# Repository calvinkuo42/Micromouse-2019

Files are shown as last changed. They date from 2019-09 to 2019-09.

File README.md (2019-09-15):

# Micromouse-2019

IEEE Micromouse project I did with Philip Kwan and Sean Chen at UCLA over the 2018-19 school year. We began with a STM32 Nucleo Development board and assembled a demo from a previously designed kit. We then programmed the hardware using C on mbed. A similar code was used to control the "mouse" we later designed ourselves (schematic and board).

Micromouse: https://en.wikipedia.org/wiki/Micromouse

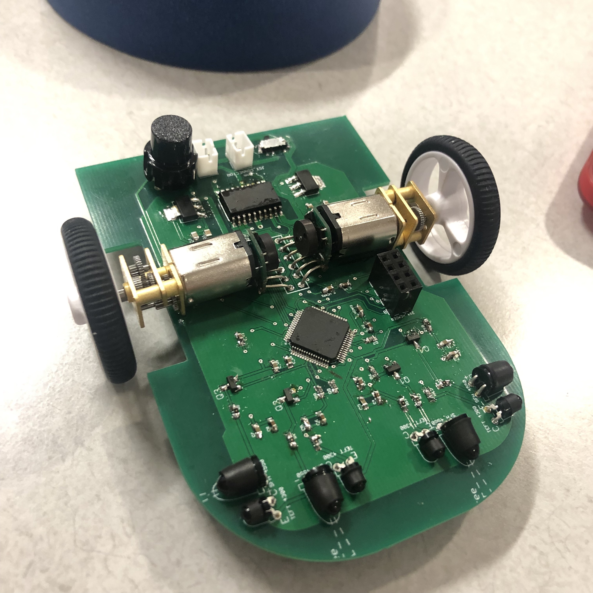
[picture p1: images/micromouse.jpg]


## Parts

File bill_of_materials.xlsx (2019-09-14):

Category | Part No. (Manufacturer) | Package | Vendor | Vendor No. | Description | Qty. | Unit Price | Total Price | Vendor Link
Transistor | SFH 309 | 5mm | Mouser | 720-SFH309 | ir_receiver | 8 | $0.39 | $3.12 | https://www.mouser.com/ProductDetail/OSRAM-Opto-Semiconductors/SFH-309
LED | SFH 4550 | 5mm | Mouser | 720-SFH4550 | ir_emitter | 10 | $0.80 | $8.00 | https://www.mouser.com/ProductDetail/OSRAM-Opto-Semiconductors/SFH-4550
H-Bridge | L293DD | so20 | Mouser | 511-L293DD | motor_driver | 2 | $3.83 | $7.66 | https://www.mouser.com/ProductDetail/STMicroelectronics/L293DD
Other IC | AZ1117EH-3.3TRG1 | so223 | Digi-Key | AZ1117EH-3.3TRG1DICT-ND | voltage_regulator | 4 | $0.43 | $1.72 | https://www.digikey.com/product-detail/en/diodes-incorporated/AZ1117EH-3.3TRG1/AZ1117EH-3.3TRG1DICT-ND/5001336
Other IC | AZ1117EH-5.0TRG1 | so223 | Digi-Key | AZ1117EH-5.0TRG1DICT-ND | voltage_regulator | 4 | $0.43 | $1.72 | https://www.digikey.com/product-detail/en/diodes-incorporated/AZ1117EH-5.0TRG1/AZ1117EH-5.0TRG1DICT-ND/5001335
Other | none | none | Pololu | 3081 | encoder | 2 | $8.95 | $17.90 | https://www.pololu.com/product/3081
MCU | STM32F405RGT6 | lqfp64 | Digi-Key | 497-11767-ND | microcontroller | 1 | $10.58 | $10.58 | https://www.digikey.com/product-detail/en/STM32F405RGT6/497-11767-ND/2754208?WT.z_slp_buy=stm_stm32f4
Other | none | none | Pololu | 2378 | motor | 2 | $16.95 | $33.90 | https://www.pololu.com/product/2378
Other | none | none | Pololu | 989 | motor_bracket | 1 | $4.99 | $4.99 | https://www.pololu.com/product/989
Transistor | CMPDM7002AHC TR | SOT-23 | Digi-Key | CMPDM7002AHCCT-ND | mosfet | 5 | $0.70 | $3.50 | https://www.digikey.com/product-detail/en/central-semiconductor-corp/CMPDM7002AHC-TR/CMPDM7002AHCCT-ND/5324492
Capacitor | C0805T105K4RACTU | 805 | Mouser | 80-C0805T105K4RACTU | capacitor | 8 | $2.06 | $16.48 | https://www.mouser.com/ProductDetail/KEMET/C0805T105K4RACTU
Capacitor | 06035J0R1PBSTR | 603 | Mouser | 581-06035J0R1PBSTR | capacitor | 8 | $1.94 | $15.52 | https://www.mouser.com/ProductDetail/AVX/06035J0R1PBSTR
Capacitor | 06035J0R1PBSTR | 603 | Mouser | 81-ZRB18AR6YA475KE5L | capacitor | 8 | $0.37 | $2.96 | https://www.mouser.com/ProductDetail/AVX/06035J0R1PBSTR
Capacitor | GRM188R6YA225KA12D | 603 | Mouser | 81-GRM188R6YA225KA2D | capacitor | 4 | $0.21 | $0.84 | https://www.mouser.com/ProductDetail/Murata-Electronics/GRM188R6YA225KA12D
Resistor | RK73H1ERTTP3301D | 402 | Mouser | 660-RK73H1ERTTP3301D | resistor | 3 | $0.41 | $1.23 | https://www.mouser.com/ProductDetail/KOA-Speer/RK73H1ERTTP3301D
Resistor | RC0201JR-071KL | 603 | Mouser | 603-RC0201JR-071KL | resistor | 12 | $1.05 | $12.60 | https://www.mouser.com/ProductDetail/Yageo/RC0201JR-071KL
Resistor | RC0201FR-0751RL | 603 | Mouser | 603-RC0201FR-0751RL | resistor | 8 | $0.10 | $0.80 | https://www.mouser.com/ProductDetail/Yageo/RC0201FR-0751RL?qs=sGAEpiMZZMvdGkrng054t219Tlw6YGVDLY9pioqn68o%3d
Resistor | RC0201JR-0747KL | 603 | Mouser | 603-RC0201JR-0747KL | resistor | 8 | $0.10 | $0.80 | https://www.mouser.com/ProductDetail/Yageo/RC0201JR-0747KL
Switch/Button | SSSS811101 | spdt | Mouser | 688-SSSS811101 | switch | 1 | $0.97 | $0.97 | https://www.mouser.com/ProductDetail/ALPS/SSSS811101
Switch/Button | SKPMANE010 | none | Mouser | 688-SKPMAN | button | 1 | $0.57 | $0.57 | https://www.mouser.com/ProductDetail/ALPS/SKPMANE010/
Headers/Connectors | S2B-PH-K-S(LF)(SN) | none | Digi-Key | 455-1719-ND | jst | 2 | $0.17 | $0.34 | https://www.digikey.com/product-detail/en/jst-sales-america-inc/S2B-PH-K-S(LF)(SN)/455-1719-ND/926626&
Headers/Connectors | none | none | Pololu | 1024 | 2x4 header | 1 | $0.59 | $0.59 | https://www.pololu.com/product/1024
 |  |  |  |  |  |  |  | $0.00
 |  |  |  |  |  |  |  | $0.00
 |  |  |  |  |  |  |  | $0.00
 |  |  |  |  |  |  |  | $0.00
 |  |  |  |  |  |  |  | $0.00
 |  |  |  |  |  |  |  | $0.00
 |  |  |  |  |  |  |  | $0.00
 |  |  |  |  |  |  |  | $0.00
 |  |  |  |  |  |  |  | $0.00
 |  |  |  |  |  |  |  | $0.00
 |  |  |  |  |  |  |  | $0.00
 |  |  |  |  |  |  |  | $0.00
 |  |  |  |  |  |  |  | $0.00
 |  |  |  |  |  |  |  | $0.00
 |  |  |  |  |  |  |  | $0.00
 |  |  |  |  |  |  |  | $0.00
 |  |  |  |  |  |  |  | $0.00
 |  |  |  |  |  |  |  | $0.00
 |  |  |  |  |  |  |  | $0.00
 |  |  |  |  |  |  |  | $0.00
 |  |  |  |  |  |  |  | $0.00
 |  |  |  |  |  |  |  | $0.00
 |  |  |  |  |  |  |  | $0.00
 |  |  |  |  |  | ADAFRUIT: | $0.0000
 |  |  |  |  |  | AMAZON: | $0.0000
 |  |  |  |  |  | DIGIKEY: | $0.0000
 |  |  |  |  |  | MOUSER: | $71.5500
 |  |  |  |  |  | POLOLU: | $57.3800
 |  |  |  |  |  | SPARKFUN: | $0.0000
 |  |  |  |  |  | TOTAL: | $128.9300

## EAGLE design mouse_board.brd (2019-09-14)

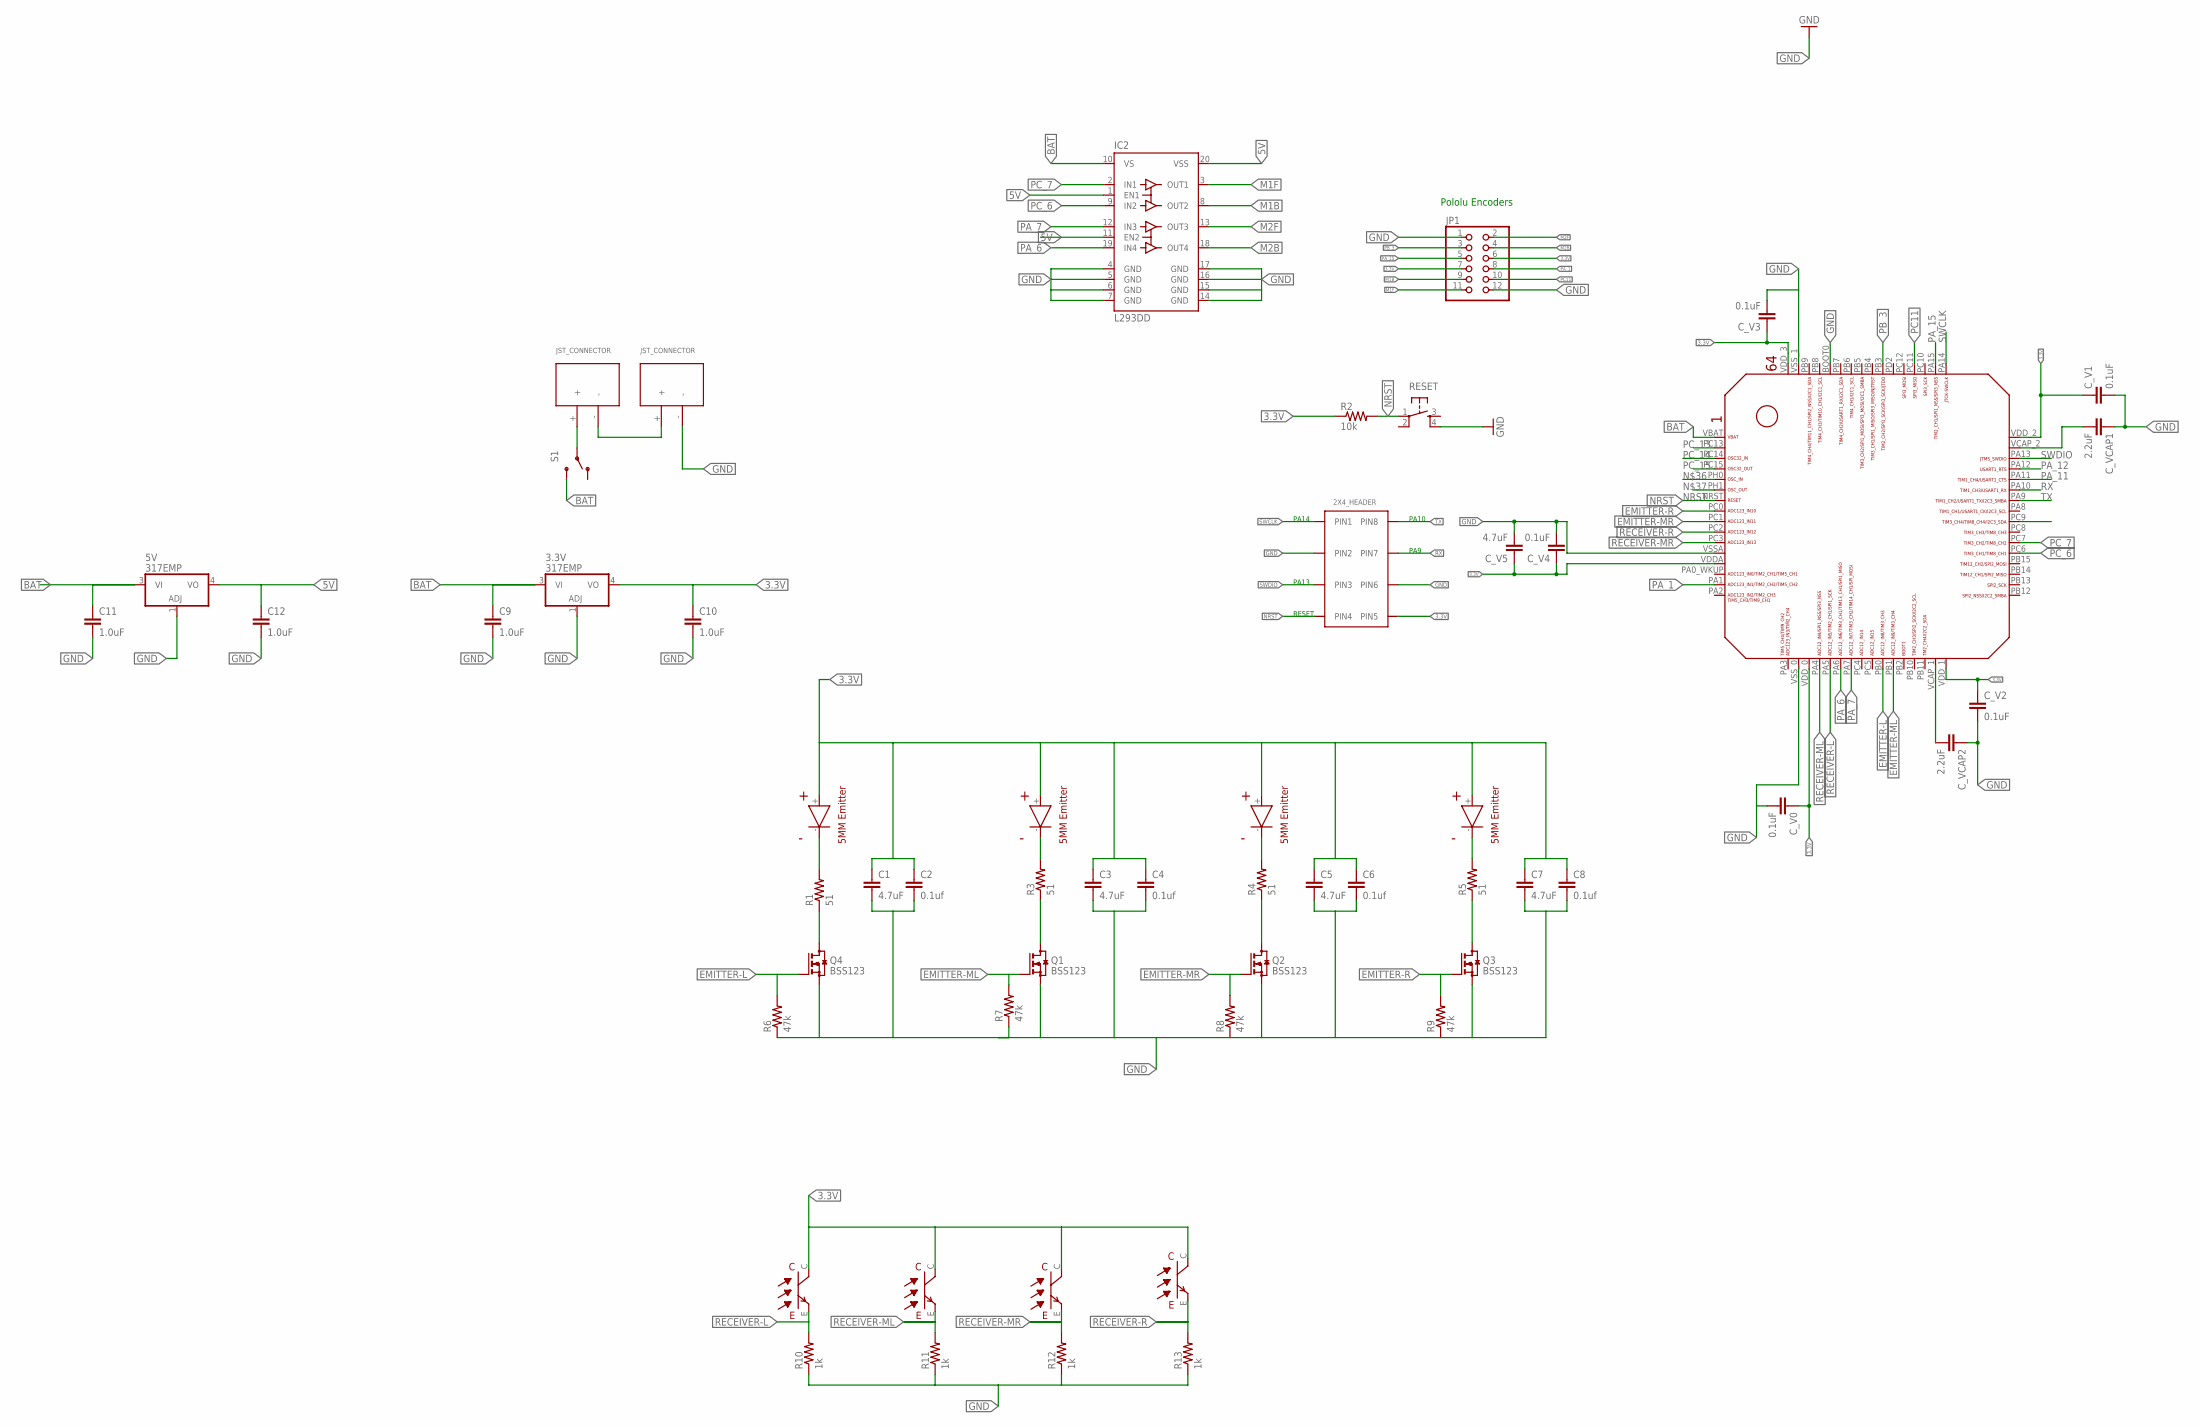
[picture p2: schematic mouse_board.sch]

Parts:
3.3V, 5V: 317EMP; SOT223
BATTERY1, BATTERY2: JST_CONNECTOR_FEMALE
C1, C3, C5, C7: 4.7uF; 0603-CAP
C2, C4, C6, C8: 0.1uf; 0603-CAP
C9, C10, C11, C12: 1.0uF; 0603-CAP
C_V0, C_V1, C_V2, C_V3, C_V4: 0.1uF; 0603-CAP
C_V5: 4.7uF; 0603-CAP
C_VCAP1, C_VCAP2: 2.2uF; 0603-CAP
IC2: L293DD; SO20
JP1: PINHD-2X6; 2X06
MCU/BLU: 2X3_HEADER
Q1, Q2, Q3, Q4: BSS123; SOT23
R1, R3, R4, R5: 51; 0603-RES
R2: 10k; 0603-RES
R6, R7, R8, R9: 47k; 0603-RES
R10, R11, R12, R13: 1k; 0603-RES
RESET: TAC_SWITCHPTH; TACTILE-PTH
S1: SWITCH-SPST-SMD-A
U$1: STM32F405/415_LQFP64
U$2, U$3, U$4, U$5: EMITTER
U$6, U$7, U$8, U$9: RECEIVER

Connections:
3.3V: 3.3V.4 (VO), C1.1, C2.1, C7.1, C8.1, C10.1, C_V0.1, C_V1.1, C_V2.1, C_V3.1, C_V4.1, C_V5.1, JP1.6, JP1.7, MCU/BLU.PIN5, R2.1, U$1.VDDA, U$1.VDD_0, U$1.VDD_1, U$1.VDD_2, U$1.VDD_3, U$2.+, U$3.+, U$4.+, U$5.+, U$6.C, U$7.C, U$8.C, U$9.C
3.3V1: Q4.3 (D), R1.1
3.3V2: Q1.3 (D), R3.1
3.3V4: Q3.3 (D), R5.1
5V: 5V.4 (VO), C12.1, IC2.1 (EN1), IC2.11 (EN2), IC2.20 (VSS)
5V1: C3.1, C4.1
5V2: C5.1, C6.1
BAT: 3.3V.3 (VI), 5V.3 (VI), C9.1, C11.1, IC2.10 (VS), S1.3 (S), U$1.VBAT
EMITTER-L: Q4.1 (G), R6.2, U$1.PB0
EMITTER-L2: R11.2, U$7.E
EMITTER-L3: R12.2, U$8.E
EMITTER-L4: R13.2, U$9.E
EMITTER-ML: Q1.1 (G), R7.2, U$1.PB1
EMITTER-MR: Q2.1 (G), R8.2, U$1.PC1
EMITTER-R: Q3.1 (G), R9.2, U$1.PC0
GND: 3.3V.1 (ADJ), 5V.1 (ADJ), BATTERY2.-, C1.2, C2.2, C3.2, C4.2, C5.2, C6.2, C7.2, C8.2, C9.2, C10.2, C11.2, C12.2, C_V0.2, C_V1.2, C_V2.2, C_V3.2, C_V4.2, C_V5.2, C_VCAP1.1, C_VCAP2.1, IC2.4 (GND), IC2.5 (GND), IC2.6 (GND), IC2.7 (GND), IC2.14 (GND), IC2.15 (GND), IC2.16 (GND), IC2.17 (GND), JP1.1, JP1.12, MCU/BLU.PIN2, MCU/BLU.PIN6, Q1.2 (S), Q2.2 (S), Q3.2 (S), Q4.2 (S), R6.1, R7.1, R8.1, R9.1, R10.1, R11.1, R12.1, R13.1, RESET.4, U$1.BOOT0, U$1.VSSA, U$1.VSS_0, U$1.VSS_1
M1B: IC2.8 (OUT2), JP1.9
M1F: IC2.3 (OUT1), JP1.11
M2B: IC2.18 (OUT4), JP1.4
M2F: IC2.13 (OUT3), JP1.2, U$1.PC9
unnamed: R1.2, U$5.-
unnamed: R3.2, U$4.-
unnamed: R4.2, U$3.-
unnamed: R5.2, U$2.-
unnamed: Q2.3 (D), R4.1
unnamed: BATTERY1.-, BATTERY2.+
unnamed: BATTERY1.+, S1.2
NRST: MCU/BLU.PIN4, R2.2, RESET.1, U$1.NRST
PA_1: JP1.8, U$1.PA1
PA_6: IC2.19 (IN4), U$1.PA6
PA_7: IC2.12 (IN3), U$1.PA7
PA_11: U$1.PA11
PA_12: U$1.PA12
PA_15: JP1.5, U$1.PA15
PB_3: JP1.3, U$1.PB3
PC11: JP1.10, U$1.PC11
PC_6: IC2.9 (IN2), U$1.PC6
PC_7: IC2.2 (IN1), U$1.PC7
PC_13: U$1.PC13
PC_14: U$1.PC14
PC_15: U$1.PC15
RECEIVER-L: R10.2, U$1.PA5, U$6.E
RECEIVER-ML: U$1.PA4
RECEIVER-MR: U$1.PC3
RECEIVER-R: U$1.PC2
RX: MCU/BLU.PIN7, U$1.PA10
SWCLK: MCU/BLU.PIN1, U$1.PA14
SWDIO: MCU/BLU.PIN3, U$1.PA13
TX: MCU/BLU.PIN8, U$1.PA9
V_C1: C_VCAP1.2, U$1.VCAP_2
V_C2: C_VCAP2.2, U$1.VCAP_1

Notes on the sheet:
PA14
PA13
RESET
PA9
PA10
Pololu Encoders

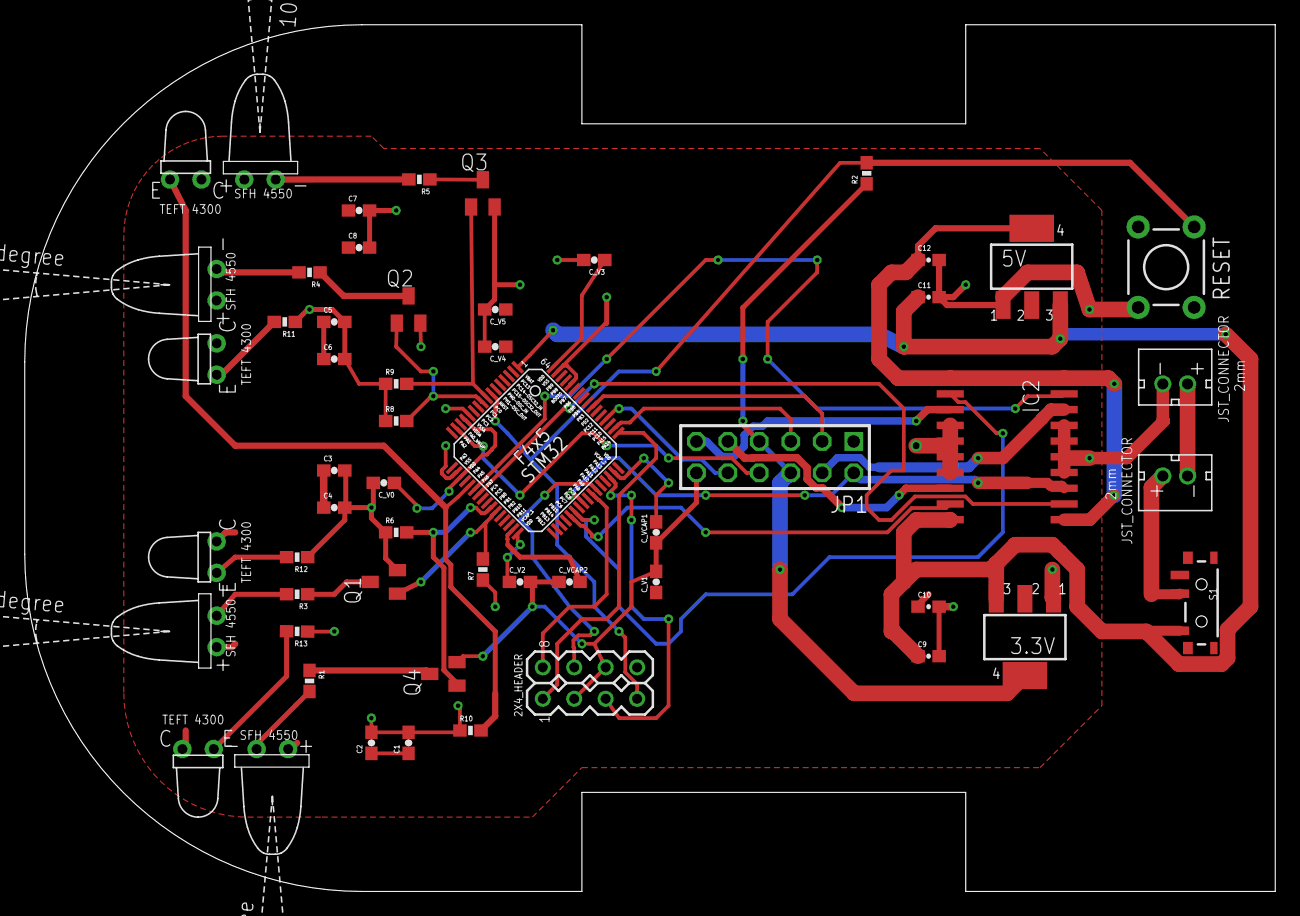
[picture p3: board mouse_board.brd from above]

Board: 2 copper layers, 101.0 x 70.0 mm, 55 parts (0 on the bottom side), 43 nets.

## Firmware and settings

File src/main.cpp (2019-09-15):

#include "globals.h"
#include "assignment2.h"
#include "assignment3.h"
#include "assignment4.h"

int main() {
    //read_encoders();
    //basic_motor_movement();
    //motor_test();
    //motors.stop();
    //test_systick();
    //drive_straight();
    //do_turns1();
    //wait(1);
    //do_turns2();
    //do_turns3();
    turn_left360();
    //turn_right360();
    //move_cells();
    //move_path();
    //left_ir_test();
    //right_ir_test();
    //all_ir_test();
}

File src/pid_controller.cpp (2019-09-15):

#include "pid_controller.h"
#include "pins.h"
#include "globals.h"
#include "read_ir.h"

PIDController::PIDController() {
    this->reset();
}

/***
 * Assignment 3
 * 
 * Implement PID!
 ***/

void PIDController::reset() volatile {    
    /**
     * You'll have a lot to keep track of. Make sure to reset all 
     * those variables here.
     **/

    m_goalW = 0;
    m_goalX = 0;
    m_countsW = 0;
    m_countsX = 0;

    m_pwmW = 0;
    m_pwmX = 0;

    m_errorW = 0;
    m_errorX = 0;
    m_errorW_old = 0;
    m_errorX_old = 0;
}

void PIDController::update() volatile {
    /**
     * Update your PID controller. This is what should be called
     * every systick, so you should call all your important
     * functions here.
     **/
     getSensorFeedback();
     //get_ir_error();
     x_controller();
     w_controller();
     updateMotorPwm();
}

void PIDController::setXGoal(int counts) {
    /**
     * Set goal for X controller.
     **/
     m_goalX = counts;
}

void PIDController::setWGoal(int counts) {
    /**
     * Set goal for W controller. Make sure to associate a turning
     * direction with a sign, e.g., positive is clockwise, negative
     * is counter-clockwise.
     **/
     m_goalW = counts;
}

void PIDController::setWCounts(int counts) {
    m_countsW = counts;
}

bool PIDController::isDone() volatile {
    /**
     * When is the PID done? Well, probably when you've reached
     * your goals...
     **/
     if (m_errorW == 0 && m_errorX == 0)
        return true;
    return false;
}

char* PIDController::getData() {
    /**
     * Use this function to print data about your PID,
     * because you can't print directly in systick!
     **/
    sprintf(buf, "goalx: %d\tgoalw: %d\tpwmx: %.3f\tpwmw: %.3f\terrorx: %d\terrorw: %d\n",
        m_goalX,
        m_goalW,
        m_pwmX,
        m_pwmW,
        m_errorX,
        m_errorW);
    return buf;
}
int PIDController::returnErrorW() {
    return m_errorW;    
}
int PIDController::returnErrorX() {
    return m_errorX;
}



/**
 * Private functions to do the internal work for PID.
 **/
void PIDController::getSensorFeedback() volatile {
    /**
     * Update sensor values, from encoders
     **/
     m_countsX = (encoders.getPulsesR() + encoders.getPulsesL())/2;
     m_countsW = encoders.getPulsesR() - encoders.getPulsesL();
}

float PIDController::get_ir_error() volatile {
    float error;

    /*
    - These MID values can be hardcoded, or maybe even calculated at some
    point in your program...
    - You may find that setting these mid values to something that doesn't
    quite correspond to the middle (e.g., MIDR slightly to the right of the
    middle rather that directly in the center), may make your Rat perform
    better. Play around with it!
    */  
    if (flash_ir(R_EMITTER, R_RECEIVER) > MIDR) {
        error = flash_ir(R_EMITTER, R_RECEIVER) - MIDR;
    }
    else if (flash_ir(L_EMITTER, L_RECEIVER) > MIDL) {
        // Make sure to change the sign for the error!
        error = MIDL - flash_ir(L_EMITTER, L_RECEIVER);
    }
    else {
        // No useful information from IR's
        error = 0;
    }

    return error;
}

void PIDController::x_controller() volatile {
    /**
     * Your X PID controller, sets m_pwmX
     **/
    m_errorX = m_goalX - m_countsX;
    m_pwmX = KpX * m_errorX + KdX * (m_errorX - m_errorX_old);
    m_errorX_old = m_errorX;
    if (isStraight) {
        if( m_pwmX > 0.2)
            m_pwmX = 0.2;
    }
    else
        m_pwmX = 0;
}

void PIDController::w_controller() volatile {
    /**
     * Your W PID controller, sets m_pwmW
     **/
     m_errorW = m_goalW - m_countsW;
     m_pwmW = KpW * m_errorW + KdW * (m_errorW - m_errorW_old); //+ get_ir_error() * IR_SCALING
     m_errorW_old = m_errorW;
}

void PIDController::updateMotorPwm() volatile {
    /**
     * Takes m_pwmX, m_pwmW, and adjusts the motors based on those values.
     **/
     motors.setRightPwm(m_pwmX + m_pwmW);
     motors.setLeftPwm(m_pwmX - m_pwmW);
}

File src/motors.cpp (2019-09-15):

#include "motors.h"
#include "mbed.h"
#include "pins.h"

PwmOut m_RF(MOTOR_RF);
PwmOut m_RB(MOTOR_RB);
PwmOut m_LF(MOTOR_LF);
PwmOut m_LB(MOTOR_LB);

/***
 * Assignment 2
 * 
 * Add logic to set the PWM based on postiive/negative number.
 ***/

void Motors::setMotorPwm(int motor, float pwm) {
    if (abs(pwm) > MAX_SPEED) {
        if (pwm > 0) pwm = MAX_SPEED;
        else if (pwm < 0) pwm = -MAX_SPEED;
    }
    else if (abs(pwm) < MIN_SPEED) {
        if (pwm > 0) pwm = MIN_SPEED;
        else if (pwm < 0) pwm = -MIN_SPEED;
    }
    
    // TODO
    // Use the "PwmOut" objects defined above
    // Hint: Stop your backwards/forward motor before going forward/backwards.
    if (pwm > 0) {
        if (motor == RIGHT_MOTOR) {
            m_RB = 0;
            m_RF = pwm;
        } else {
            m_LB = 0;
            m_LF = pwm;
        }
    } else {
        if (motor == RIGHT_MOTOR) {
            m_RF = 0;
            m_RB = -pwm;
        } else {
            m_LF = 0;
            m_LB = -pwm;
        }
    }
}

Motors::Motors() {
    // DO NOT initialize PWM!!! It breaks the mouse.
}

void Motors::stop() {
    setRightPwm(0);
    setLeftPwm(0);   
}

void Motors::setRightPwm(float pwm) {
    m_rpwm = pwm;
    setMotorPwm(RIGHT_MOTOR, pwm);
}

void Motors::setLeftPwm(float pwm) {
    m_lpwm = pwm;
    setMotorPwm(LEFT_MOTOR, pwm);
}

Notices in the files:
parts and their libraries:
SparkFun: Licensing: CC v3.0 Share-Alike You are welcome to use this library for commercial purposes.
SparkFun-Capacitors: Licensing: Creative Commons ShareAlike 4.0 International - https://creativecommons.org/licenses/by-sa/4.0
